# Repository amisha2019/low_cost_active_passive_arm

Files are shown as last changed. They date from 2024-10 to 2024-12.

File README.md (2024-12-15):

# Low-Cost Robot Arm 

This repository contains the files to build and control a low-cost robot arm that costs about $250. You can also build a second robot arm (the leader arm) to control the other arm (the follower arm) that costs about $180, for a total of $430. The design of the leader is inspired by the [GELLO project](https://github.com/wuphilipp/gello_mechanical) but is simpler to build. Such a robot arm is well suited for [robot learning](https://x.com/alexkoch_ai/status/1756500716854841835?s=20). Two of those arms are also capable of [folding clothes](https://x.com/alexkoch_ai/status/1772750496174149708?s=20).

This robot arm uses Dynamixel XL430 and Dynamixel XL330 servo motors. The XL430 motors are almost twice as strong and are used for the first two joints.
The XL330 motors are weaker but weigh only 18g each. This makes the arm very lightweight and fast.
Dynamixel sells the U2D2 adapter to connect the servos to a computer. However, this is very expensive and the latency is very high. This build uses another cheaper adapter board instead.
The robot arm can be controlled with the Dynamixel SDK: ```pip install dynamixel-sdk```

Robot Arm

## Follower Arm

### Required Materials

| Part | Cost | Buying link | Specs |
|---|---|---| --- |
| 2x Dynamixel XL430-W250 | $100 | https://www.robotis.us/dynamixel-xl430-w250-t/ | https://emanual.robotis.com/docs/en/dxl/x/xl430-w250/ |
| 4x Dynamixel XL330-M288 | $96  | https://www.robotis.us/dynamixel-xl330-m288-t/ | https://emanual.robotis.com/docs/en/dxl/x/xl330-m288/|
| XL330 Idler Wheel | $10  | https://www.robotis.us/fpx330-h101-4pcs-set/ | **Note**: pack of four; three needed for  longer version pictured above (with elbow-to-wrist extension), two needed for shorter version|
| XL430 Idler Wheel | $7 | https://www.robotis.us/hn11-i101-set/ | |
| Waveshare Serial Bus Servo Driver Board | $10  | https://a.co/d/7C3RUYU | |
| Voltage Reducer | $10 | https://a.co/d/cy02ADW | **Note**: pack of six, only one needed per follower arm |
| 12V Power Supply | $12  | https://a.co/d/40o8uMN | |
| Table Clamp | $6 | https://a.co/d/4KEiYdV | |
| Wires | $7 | https://a.co/d/hQfk2cb | |
| Total | $258 | | |

There is usually a 10% discount code for the Robotis shop. It might also help to add some grip tape to the gripper (e.g. https://a.co/d/dW7BnEN). A USB-C cable is necessary to connect the servo driver board to a computer.

### Assembly

1. Print all parts with a 3D printer
   1. The STL files are in `hardware/follower/stl`
   2. The parts are designed to be easy to print; only the moving part of the gripper needs supports
2. Scanning motors
   1. Connect the driver board to a computer (should work with Linux and MacOS)
   2. Figure out the device name (e.g. tty.usbmodem57380045631 for MacOS): ```ls /dev/tty.*```
   3. Scan each motor individually with [Dynamixel Wizard](https://emanual.robotis.com/docs/en/software/dynamixel/dynamixel_wizard2/)
      1. Set the baudrate to 1M for all motors
      2. Set the servo IDs to 1 for the shoulder to 5 (6 if using the elbow-to-wrist extension) for the gripper servo
3. Assembly
   1. Assemble the arm without the base
      1. Make sure that the servos are fixed in the same position as in the CAD
      2. The servo horn should be in the default position when screwed in
   2. Solder wires onto voltage reducer; input should be connected to female connectors and the output to male connectors
   3. Screw the voltage reducer and the servo driver board onto the base
   4. Screw the base onto the arm
   5. Connect D, V, and G ports on the driver board to the shoulder rotation servo
   6. Connect the shoulder rotation servo to the shoulder lift servo
   7. Connect the input for the voltage reducer to V and G ports on the driver board
   8. Connect the output of the voltage reducer and the remaining D port of the driver board to the elbow servo
   9. Connect the driver board to the power supply
   10. Connect to an XL330 servo and view the input voltage on Dynamixel Wizard, then adjust the screw on the voltage reducer until the input voltage is 5V

## Leader Arm

### Required Materials

| Part | Cost | Buying link | Specs |
|---|---| --- | --- |
| 6x Dynamixel XL330-M077 | $144 |  https://www.robotis.us/dynamixel-xl330-m077-t/ | https://emanual.robotis.com/docs/en/dxl/x/xl330-m077/|
| XL330 Frame | $7 | https://www.robotis.us/fpx330-s101-4pcs-set/ | |
| XL330 Idler Wheel | $10  | https://www.robotis.us/fpx330-h101-4pcs-set/ | **Note**: pack of four; three needed for longer version (with elbow-to-wrist extension), two needed for shorter version pictured below |
| Waveshare Serial Bus Servo Driver Board | $10  | https://a.co/d/7C3RUYU | |
| 5V Power Supply | $6 | https://a.co/d/5u90NVp | |
| Table Clamp | $6 | https://a.co/d/4KEiYdV | |
| Total | $183 | | |

### Assembly

The assembly of the leader arm is simpler since all motors use 5V. The gripper is replace by a handle and a trigger. During use, a small torque can be applied to the trigger so that it opens by default. The GELLO design uses a spring for this purpose but it is much more difficult to assemble.
The `teleoperation.py` script can be used to test the arms. However, the device names might have to be adjusted.

## Simulation
A basic simulation environment in MuJoCo is available by running `simulation.py`.

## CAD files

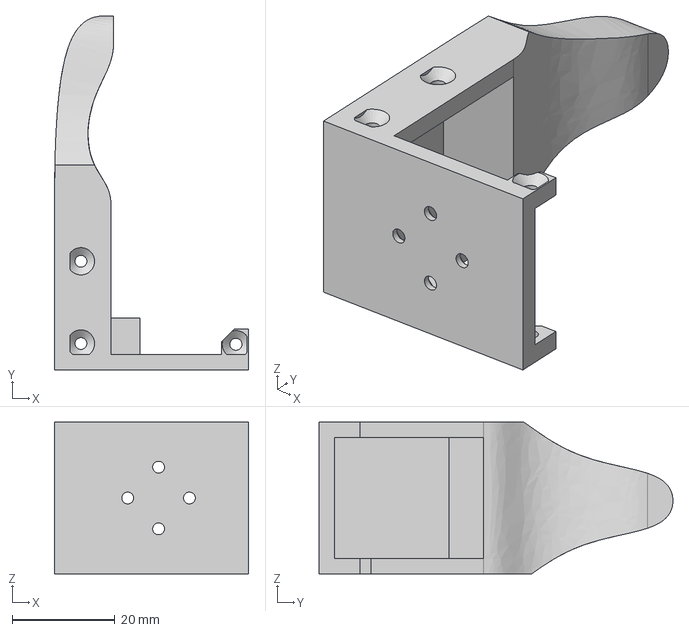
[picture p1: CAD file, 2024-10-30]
hardware/follower/step/gripper_static_part.step
37.7 x 68.9 x 29.5 mm

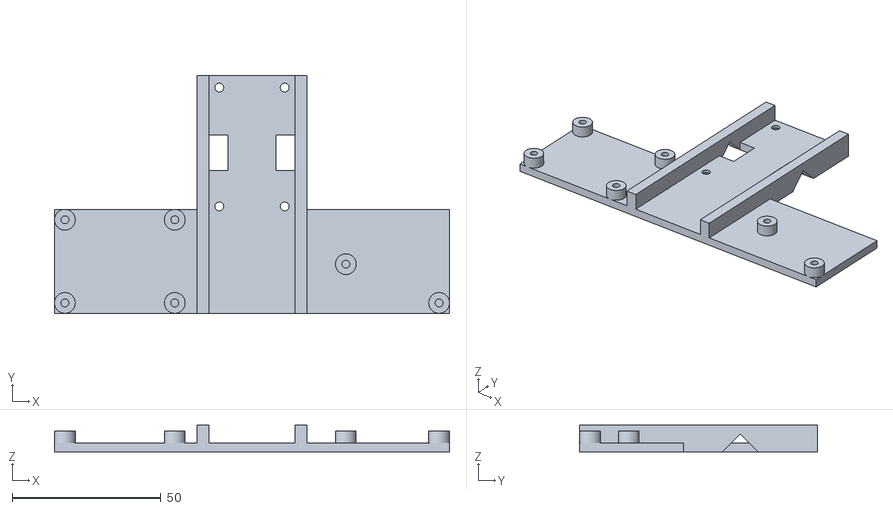
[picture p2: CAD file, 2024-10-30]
hardware/follower/stl/base.stl
133.0 x 80.0 x 9.00

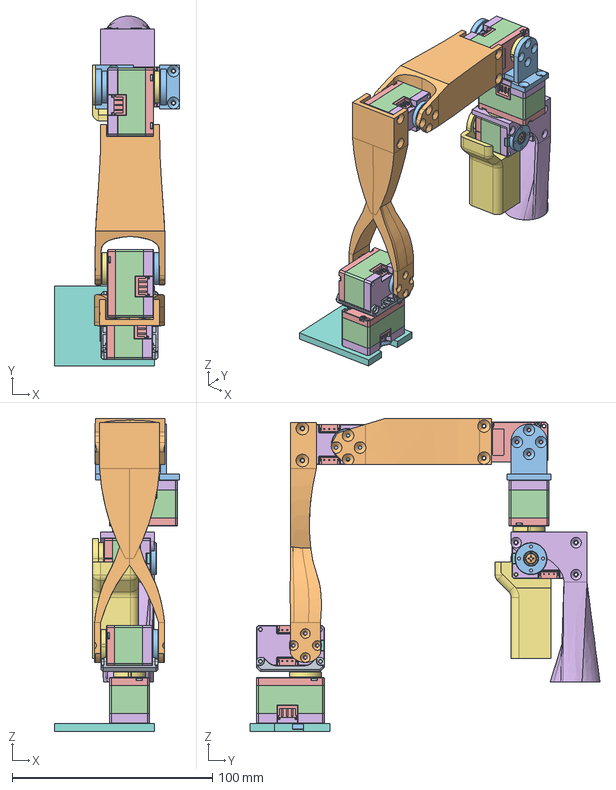
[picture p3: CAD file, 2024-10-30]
hardware/leader/step/leader_arm.step
62.7 x 175.0 x 156.5 mm
Servo Connector redesign
shoulder_rotation
DC15_A01_CASE_M_DUMMY x 6
DC15_A01_CASE_F_DUMMY x 6
DC15_A01_CASE_B_DUMMY x 6
DC15_A01_HORN_DUMMY x 6
DC15_A01_LED_CAP2_DUMMY x 6
PHS_1_7X20_5_DC10 x 24
BTS2_M2_6X8 x 12
DC15_A01_HORN_IDLE2_DUMMY x 6
DC15_A01_IDLE_CAP_DUMMY x 6
B3B-EH x 12
handle
trigger
base
fpx330-s101
connector

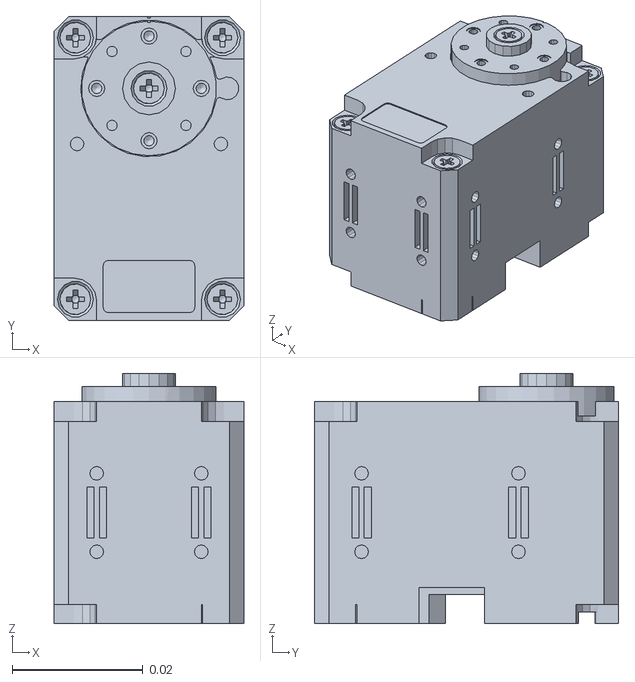
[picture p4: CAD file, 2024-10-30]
simulation/gello_active/assets/gello_active/xl430_2.STL
0.029 x 0.0465 x 0.0383

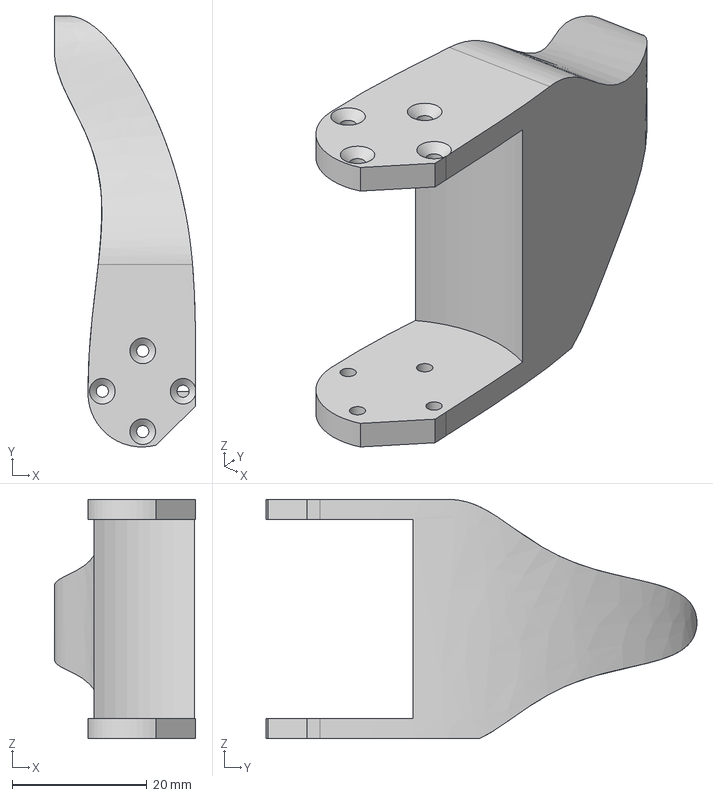
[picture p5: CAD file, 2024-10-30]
hardware/follower/step/gripper_moving_part.step
21.0 x 64.0 x 35.5 mm

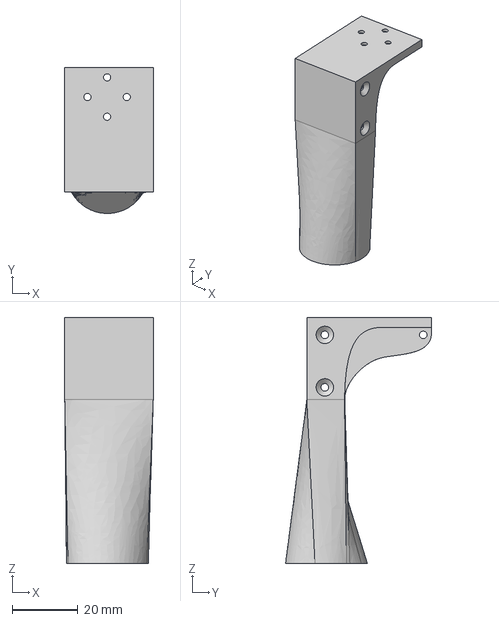
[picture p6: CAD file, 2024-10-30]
hardware/leader/step/gripper_handle.step
27.0 x 44.5 x 75.0 mm

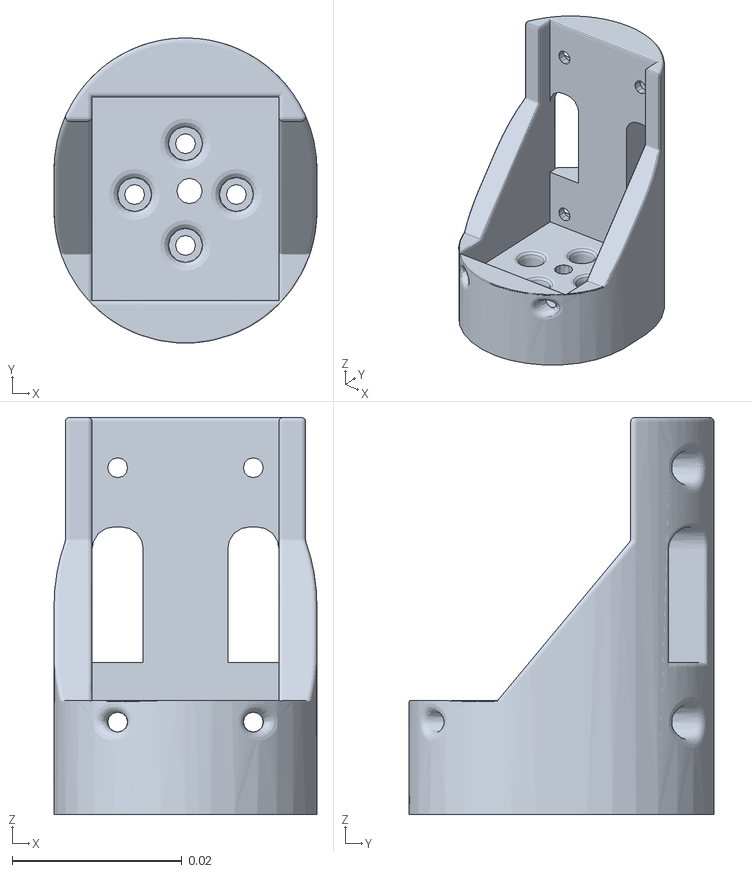
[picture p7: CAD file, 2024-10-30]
simulation/gello_active/assets/gello_active/L4.STL
0.031 x 0.036 x 0.0468

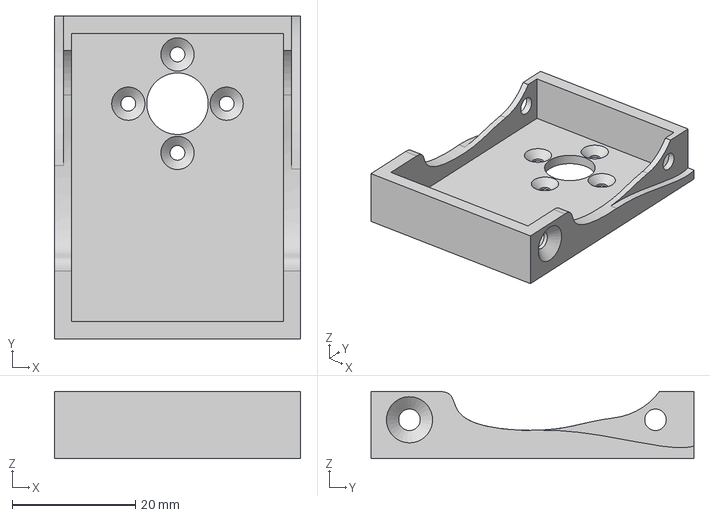
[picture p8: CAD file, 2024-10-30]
hardware/follower/step/shoulder_rotation.step
40.0 x 52.5 x 10.9 mm

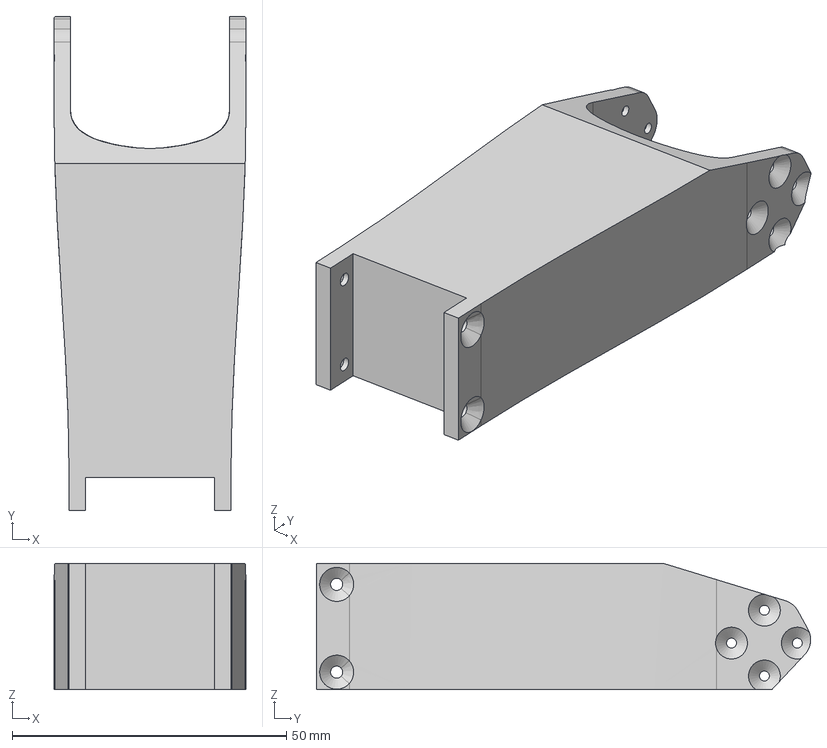
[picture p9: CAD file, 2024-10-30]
hardware/leader/step/elbow_to_wrist_extension.step
35.0 x 90.1 x 23.0 mm

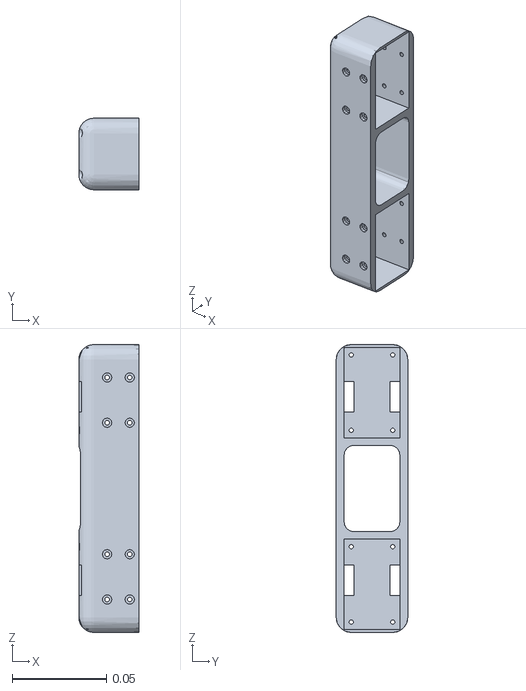
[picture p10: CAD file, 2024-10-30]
simulation/gello_active/assets/gello_active/L2.STL
0.032 x 0.038 x 0.153

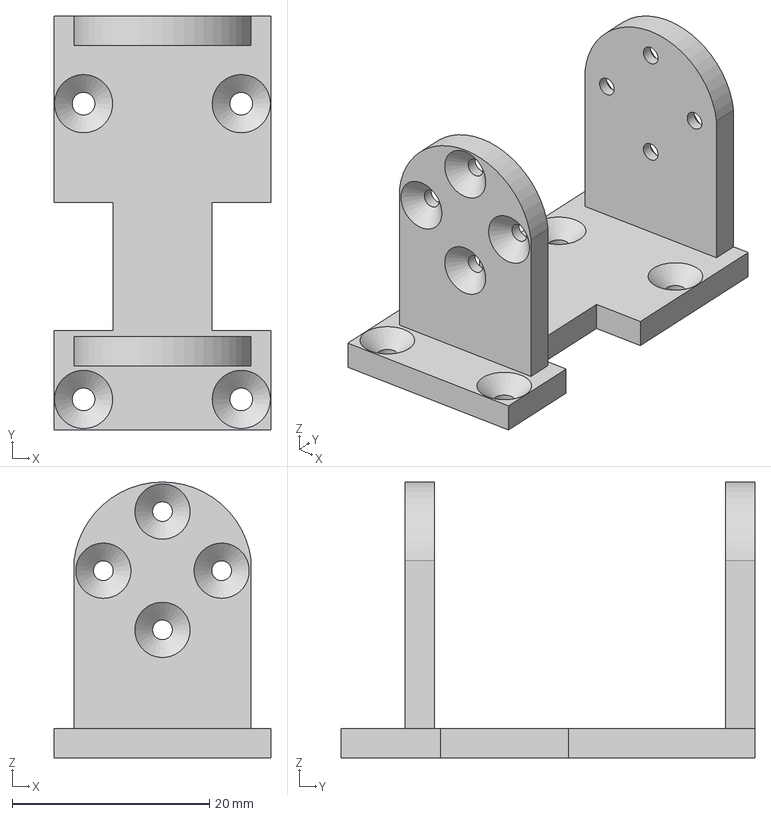
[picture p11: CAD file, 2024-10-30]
hardware/follower/step/elbow_to_wrist.step
22.0 x 42.0 x 28.0 mm

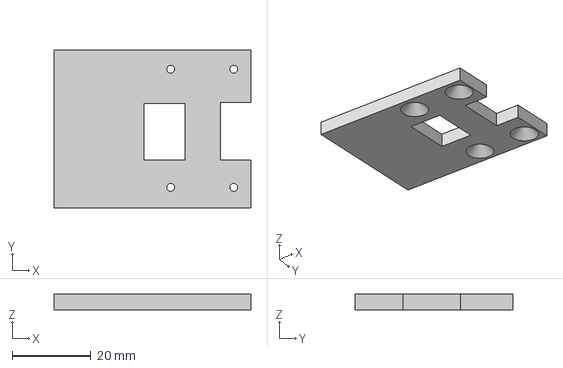
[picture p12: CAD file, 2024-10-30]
hardware/leader/step/base.step
50.0 x 40.0 x 4.00 mm

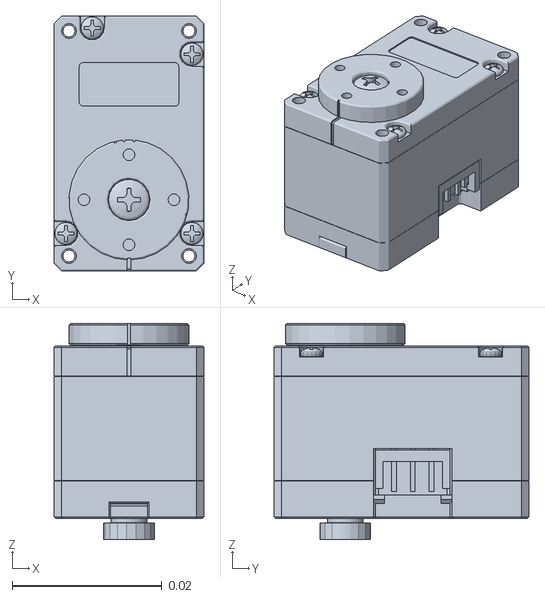
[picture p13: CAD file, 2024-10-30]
simulation/gello_active/assets/gello_active/xl330_3.STL
0.02 x 0.034 x 0.0288

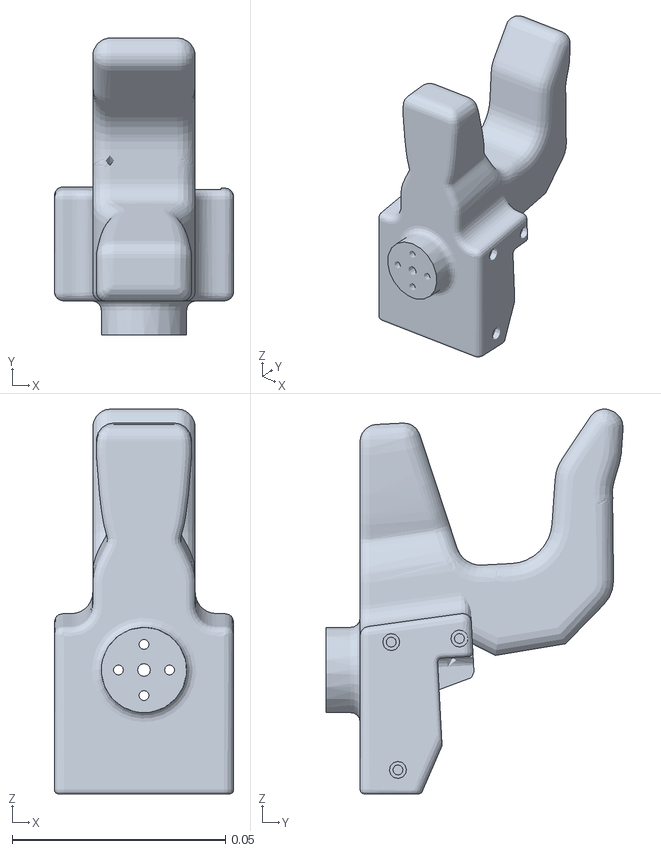
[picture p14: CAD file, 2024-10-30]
simulation/gello_active/assets/gello_active/end_effector.STL
0.042 x 0.0696 x 0.0902

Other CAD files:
hardware/leader/step/elbow_to_wrist.step
hardware/follower/step/arm.step
hardware/leader/step/shoulder_to_elbow.step
hardware/follower/follower_arm.f3z
hardware/follower/step/shoulder_to_elbow.step
hardware/follower/stl/elbow_to_wrist.stl
hardware/follower/stl/elbow_to_wrist_extension.stl
hardware/follower/stl/gripper_moving_part.stl
hardware/follower/stl/gripper_static_part.stl
hardware/follower/stl/shoulder_rotation.stl
hardware/follower/stl/shoulder_to_elbow.stl
hardware/leader/leader_arm.f3z
hardware/leader/step/gripper_trigger.step
hardware/leader/stl/base.stl
hardware/leader/stl/elbow_to_wrist.stl
hardware/leader/stl/elbow_to_wrist_extension.stl
hardware/leader/stl/gripper_handle.stl
hardware/leader/stl/gripper_trigger.stl
hardware/leader/stl/shoulder_to_elbow.stl
simulation/gello_active/assets/gello_active/L1.STL
simulation/gello_active/assets/gello_active/L3.STL
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

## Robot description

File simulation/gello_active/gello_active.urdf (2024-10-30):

<?xml version="1.0" encoding="utf-8"?>
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
<robot name="gello_active">
  <link name="base_link">
    <inertial>
      <origin xyz="0.00607992357022163 0.00301681012562898 -0.0120084237052049" rpy="0 0 0" />
      <mass value="0.141701823329413" />
      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
    </inertial>
    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
  </link>
  <link name="xl430_1">
    <inertial>
      <origin xyz="1.5967816055059E-05 -0.0231678735095451 0.189804632480122" rpy="0 0 0" />
      <mass value="0.0422899908141637" />
      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
    </inertial>
    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
  </link>
  <joint name="base_fix_joint" type="fixed">
    <origin xyz="0.031148 0.02289 -0.18013" rpy="0 0 0" />
    <parent link="base_link" />
    <child link="xl430_1" />
    <axis xyz="0 0 0" />
  </joint>
  <link name="L1">
    <inertial>
      <origin xyz="0.0131095359774512 0.0200185962795386 3.85052656877438E-08" rpy="0 0 0" />
      <mass value="0.0422302330046642" />
      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
    </inertial>
    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
  </link>
  <joint name="shoulder_pan_joint" type="continuous">
    <origin xyz="0 -0.011 0.20764" rpy="1.5708 0 1.5588" />
    <parent link="xl430_1" />
    <child link="L1" />
    <axis xyz="0 1 0" />
  </joint>
  <link name="xl430_2">
    <inertial>
      <origin xyz="1.59678160428812E-05 -0.0121678735095403 -0.0205450583333916" rpy="0 0 0" />
      <mass value="0.0422899908141372" />
      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
    </inertial>
    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
  </link>
  <joint name="shoulder_lift_joint" type="continuous">
    <origin xyz="0.03915 0.021935 0" rpy="1.5708 1.5675 -1.5708" />
    <parent link="L1" />
    <child link="xl430_2" />
    <axis xyz="0 0 1" />
  </joint>
  <link name="L2">
    <inertial>
      <origin xyz="0.0177542994227649 2.65439271743273E-08 -0.0453750285135328" rpy="0 0 0" />
      <mass value="0.0546858829355452" />
      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
    </inertial>
    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
  </link>
  <joint name="L2_fix_joint_1" type="fixed">
    <origin xyz="0 -0.0178 -0.04565" rpy="1.5708 -1.5708 3.14" />
    <parent link="xl430_2" />
    <child link="L2" />
    <axis xyz="0 0 0" />
  </joint>
  <link name="xl430_3">
    <inertial>
      <origin xyz="1.59678160644369E-05 -0.0231678735095394 0.189804632480152" rpy="0 0 0" />
      <mass value="0.0422899908141366" />
      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
    </inertial>
    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
  </link>
  <joint name="L2_fix_joint_2" type="fixed">
    <origin xyz="-0.1647 0 -0.11955" rpy="-1.5708 0 -1.5708" />
    <parent link="L2" />
    <child link="xl430_3" />
    <axis xyz="0 0 0" />
  </joint>
  <link name="L3">
    <inertial>
      <origin xyz="-0.0301727625382926 7.29364901808083E-09 0.0367965289329686" rpy="0 0 0" />
      <mass value="0.0492342604004969" />
      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
    </inertial>
    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
  </link>
  <joint name="elbow_joint" type="continuous">
    <origin xyz="0 -0.011 0.20635" rpy="3.1391 1.5708 0" />
    <parent link="xl430_3" />
    <child link="L3" />
    <axis xyz="1 0 0" />
  </joint>
  <link name="xl330_1">
    <inertial>
      <origin xyz="0.075420933410812 0.0347673256207063 0.382628050770604" rpy="0 0 0" />
      <mass value="0.0152279846230564" />
      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
    </inertial>
    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
  </link>
  <joint name="L3_fix_joint" type="fixed">
    <origin xyz="-0.4171 0.075425 0.13419" rpy="-1.5708 0 -1.5708" />
    <parent link="L3" />
    <child link="xl330_1" />
    <axis xyz="0 0 0" />
  </joint>
  <link name="L4">
    <inertial>
      <origin xyz="-0.000477072229915942 0.00401650330059737 0.0139990913771146" rpy="0 0 0" />
      <mass value="0.0140660643273876" />
      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
    </inertial>
    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
  </link>
  <joint name="wrist1_joint" type="continuous">
    <origin xyz="0.075425 0.027592 0.39603" rpy="0 0 -0.0253" />
    <parent link="xl330_1" />
    <child link="L4" />
    <axis xyz="0 0 1" />
  </joint>
  <link name="xl330_2">
    <inertial>
      <origin xyz="0.0754209334106387 0.0347673256204681 0.38262805076857" rpy="0 0 0" />
      <mass value="0.0152279846189667" />
      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
    </inertial>
    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
  </link>
  <joint name="L4_fix_joint" type="fixed">
    <origin xyz="0.07495 0.38155 0.061433" rpy="-1.5708 0 -3.1416" />
    <parent link="L4" />
    <child link="xl330_2" />
    <axis xyz="0 0 0" />
  </joint>
  <link name="L5">
    <inertial>
      <origin xyz="-0.00366525305716781 -0.0146866156468189 -5.58749708168271E-08" rpy="0 0 0" />
      <mass value="0.0143126365472127" />
      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
    </inertial>
    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
  </link>
  <joint name="wrist2_joint" type="continuous">
    <origin xyz="0.075425 0.027592 0.39554" rpy="-1.5708 0 0.0015559" />
    <parent link="xl330_2" />
    <child link="L5" />
    <axis xyz="0 1 0" />
  </joint>
  <link name="xl330_3">
    <inertial>
      <origin xyz="0.0754209334109733 0.034767325620958 0.382628050772475" rpy="0 0 0" />
      <mass value="0.0152279846267835" />
      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
    </inertial>
    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
  </link>
  <joint name="L5_fix_joint" type="fixed">
    <origin xyz="-0.38197 -0.06135 0.075425" rpy="0 1.5708 0" />
    <parent link="L5" />
    <child link="xl330_3" />
    <axis xyz="0 0 0" />
  </joint>
  <link name="end_effector">
    <inertial>
      <origin xyz="-0.000754673739559147 0.0314156499838131 0.019054370079741" rpy="0 0 0" />
      <mass value="0.0630826138989227" />
      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
    </inertial>
    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
  </link>
  <joint name="end_effector_joint" type="continuous">
    <origin xyz="0.075425 0.027592 0.39645" rpy="1.5708 0 -0.0035937" />
    <parent link="xl330_3" />
    <child link="end_effector" />
    <axis xyz="0 1 0" />
  </joint>
</robot>

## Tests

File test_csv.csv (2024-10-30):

shoulder_pan_angle | shoulder_lift_angle | elbow_angle | wrist1_angle | wrist2_angle | wrist3_angle | end_eff_x | end_eff_y | end_eff_z | end_eff_roll | end_eff_pitch | end_eff_yaw | end_eff_w | end_eff_xq | end_eff_yq | end_eff_zq | gripper_pos
-1.595508877431051 | -1.5983616314330042 | -1.596028447151184 | -1.5511920370957633 | 1.5769364833831787 | 1.5969127416610718 | 0.023529411764705882 | -0.13866740569922242 | -0.2984518748763483 | 0.28981716946903796 | -2.2654083880941385 | -2.149327141193777 | -0.04694173033470125 | 0.023529411764705882 | 0.023529411764705882
-1.5942290464984339 | -1.5983792744078578 | -1.59576416015625 | -1.5510205545327445 | 1.5769202709197998 | 1.596408486366272 | 0.023529411764705882 | -0.1381336836522397 | -0.2987266204661276 | 0.28984151784709505 | -2.2629313974454437 | -2.1521077248571445 | -0.04675525879796806 | 0.023529411764705882 | 0.023529411764705882
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

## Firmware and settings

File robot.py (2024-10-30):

#!/usr/bin/env python3
import numpy as np
from dynamixel import Dynamixel, OperatingMode, ReadAttribute
import time
from dynamixel_sdk import GroupSyncRead, GroupSyncWrite, DXL_LOBYTE, DXL_HIBYTE, DXL_LOWORD, DXL_HIWORD
from enum import Enum, auto
from typing import Union

class MotorControlType(Enum):
    PWM = auto()
    POSITION_CONTROL = auto()
    DISABLED = auto()
    UNKNOWN = auto()

class Robot:
    def __init__(self, dynamixel, baudrate=1000000, servo_ids=[1, 2, 3, 4, 5]):
        self.servo_ids = servo_ids
        self.dynamixel = dynamixel
        
        self.position_reader = GroupSyncRead(
            self.dynamixel.portHandler,
            self.dynamixel.packetHandler,
            ReadAttribute.POSITION.value,
            4
        )
        for id in self.servo_ids:
            self.position_reader.addParam(id)

        self.velocity_reader = GroupSyncRead(
            self.dynamixel.portHandler,
            self.dynamixel.packetHandler,
            ReadAttribute.VELOCITY.value,
            4
        )
        for id in self.servo_ids:
            self.velocity_reader.addParam(id)

        self.pos_writer = GroupSyncWrite(
            self.dynamixel.portHandler,
            self.dynamixel.packetHandler,
            self.dynamixel.ADDR_GOAL_POSITION,
            4
        )
        for id in self.servo_ids:
            self.pos_writer.addParam(id, [2048])

        self.pwm_writer = GroupSyncWrite(
            self.dynamixel.portHandler,
            self.dynamixel.packetHandler,
            self.dynamixel.ADDR_GOAL_PWM,
            2
        )
        for id in self.servo_ids:
            self.pwm_writer.addParam(id, [2048])

        self._disable_torque()
        self.motor_control_state = MotorControlType.DISABLED

    def read_position(self, tries=2):
        result = self.position_reader.txRxPacket()
        if result != 0:
            if tries > 0:
                return self.read_position(tries=tries - 1)
            else:
                print("failed to read position!!!!!!!!!!!!!!!!!!!!!!!!!!!!!")
        positions = []
        for id in self.servo_ids:
            position = self.position_reader.getData(id, ReadAttribute.POSITION.value, 4)
            if position > 2 ** 31:
                position -= 2 ** 32
            positions.append(position)
        return positions

    def read_velocity(self):
        self.velocity_reader.txRxPacket()
        velocities = []
        for id in self.servo_ids:
            velocity = self.velocity_reader.getData(id, ReadAttribute.VELOCITY.value, 4)
            if velocity > 2 ** 31:
                velocity -= 2 ** 32
            velocities.append(velocity)
        return velocities

    def set_goal_pos(self, action):
        if self.motor_control_state is not MotorControlType.POSITION_CONTROL:
            self._set_position_control()
        for i, motor_id in enumerate(self.servo_ids):
            data_write = [DXL_LOBYTE(DXL_LOWORD(action[i])),
                          DXL_HIBYTE(DXL_LOWORD(action[i])),
                          DXL_LOBYTE(DXL_HIWORD(action[i])),
                          DXL_HIBYTE(DXL_HIWORD(action[i]))]
            self.pos_writer.changeParam(motor_id, data_write)
        self.pos_writer.txPacket()

    def set_pwm(self, action):
        if self.motor_control_state is not MotorControlType.PWM:
            self._set_pwm_control()
        for i, motor_id in enumerate(self.servo_ids):
            data_write = [DXL_LOBYTE(DXL_LOWORD(action[i])),
                          DXL_HIBYTE(DXL_LOWORD(action[i]))]
            self.pwm_writer.changeParam(motor_id, data_write)
        self.pwm_writer.txPacket()

    def set_trigger_torque(self):
        self.dynamixel._enable_torque(self.servo_ids[-1])
        self.dynamixel.set_pwm_value(self.servo_ids[-1], 200)

    def limit_pwm(self, limit: Union[int, list, np.ndarray]):
        if isinstance(limit, int):
            limits = [limit] * 5
        else:
            limits = limit
        self._disable_torque()
        for motor_id, limit in zip(self.servo_ids, limits):
            self.dynamixel.set_pwm_limit(motor_id, limit)
        self._enable_torque()

    def _disable_torque(self):
        print(f'disabling torque for servos {self.servo_ids}')
        for motor_id in self.servo_ids:
            self.dynamixel._disable_torque(motor_id)

    def _enable_torque(self):
        print(f'enabling torque for servos {self.servo_ids}')
        for motor_id in self.servo_ids:
            self.dynamixel._enable_torque(motor_id)

    def _set_pwm_control(self):
        self._disable_torque()
        for motor_id in self.servo_ids:
            self.dynamixel.set_operating_mode(motor_id, OperatingMode.PWM)
        self._enable_torque()
        self.motor_control_state = MotorControlType.PWM

    def _set_position_control(self):
        self._disable_torque()
        for motor_id in self.servo_ids:
            self.dynamixel.set_operating_mode(motor_id, OperatingMode.POSITION)
        self._enable_torque()
        self.motor_control_state = MotorControlType.POSITION_CONTROL

if __name__ == "__main__":
    robot = Robot(dynamixel=Dynamixel(device_name='/dev/tty.usbmodem57380045631'))
    robot._disable_torque()
    for _ in range(10000):
        s = time.time()
        pos = robot.read_position()
        elapsed = time.time() - s
        print(f'read took {elapsed} pos {pos}')

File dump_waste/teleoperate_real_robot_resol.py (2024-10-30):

from robot import Robot
from dynamixel import Dynamixel
from get_hardware_offset import ArmOffset
import numpy as np
import time

leader_device= "/dev/serial/by-id/usb-FTDI_USB__-__Serial_Converter_FT8ISI2Y-if00-port0"
follower_device = "/dev/serial/by-id/usb-FTDI_USB__-__Serial_Converter_FT8J0W3F-if00-port0"

## Follower Arm Start pos correction
home_pos_correction = np.array([-1.57, 1.57,  3.14, -1.57, -3.14,  0])

## ----- Activate Leader Arm ---------
# leader_armoffset = ArmOffset(device_name=leader_device, baudrate=57600)
# leader_correction_joints = leader_armoffset.correction_joints
# leader_dynamixel = Dynamixel.Config(baudrate=57600, device_name=leader_device).instantiate()
# for i in range(1, 7):
#     leader_dynamixel.set_velocity_limit(i, 10)

## ----- Activate Follower Arm ---------
# follower_armoffset = ArmOffset(device_name=follower_device, baudrate=57600)
# follower_correction_joints = follower_armoffset.correction_joints
follower_dynamixel = Dynamixel.Config(baudrate=57600, device_name=follower_device).instantiate()

# leader = Robot(leader_dynamixel, servo_ids=[1, 2, 3, 4, 5, 6])
for i in range(1, 7):
    follower_dynamixel.set_velocity_limit(i, 10)
follower = Robot(follower_dynamixel, servo_ids=[1, 2, 3, 4, 5, 6])


def resol_2_rad(angles_resol):
    angles_rad = (angles_resol / 2048 - 1) * 3.14
    angles_rad[1] = -angles_rad[1]
    angles_rad[3] = -angles_rad[3]
    angles_rad[4] = -angles_rad[4]
    return angles_rad

def rad_2_resol(angles_rad):
    angles_rad[1] = -angles_rad[1]
    angles_rad[3] = -angles_rad[3]
    angles_rad[4] = -angles_rad[4]
    angles_resol = (angles_rad / 3.14 + 1) * 2048
    return angles_resol

def get_angles_to_publish_rad(angles_rad):
    corrected_joint_rad = angles_rad + home_pos_correction
    corrected_joint_rad[1] = -corrected_joint_rad[1]
    corrected_joint_rad[3] = -corrected_joint_rad[3]
    corrected_joint_rad[4] = -corrected_joint_rad[4]
    return corrected_joint_rad

# def read_leader_position():
#     global leader_joints
#     leader_joints = leader.read_position()
#     leader_joints = np.array(leader_joints)        
#     leader_joints_rad = resol_2_rad(leader_joints)
#     print("Actual resol: ", leader_joints)
#     print("Actual angle: ", leader_joints_rad)
#     leader_joints_rad = (leader_joints_rad - leader_correction_joints)
#     # leader_joints_rad_ = [math.fmod(x, 3.14) for x in leader_joints_rad]
#     print("Actual corrected angle: ", leader_joints_rad)

#     return leader_joints_rad

def set_follower_position(joints_rad):
    # Correct the radians of the follower
    pass

def go_to_start_position():
    start_pos = np.array([-1.57, -1.57, -2, -1.57, 1.57, 1.57])

    # Correct the radians of the leader
    corrected_joint_rad = get_angles_to_publish_rad(start_pos)
    follower_joints_resol = np.array(rad_2_resol(corrected_joint_rad), dtype=int)
    
    print("reading: ", follower.read_position())
    # leader_joints_rad = resol_2_rad(np.array(follower.read_position()))
    # print("Reding rad: ", leader_joints_rad)

    print("Joints to publish rad: ", corrected_joint_rad)
    print("Joints to publish: ", (follower_joints_resol))
    
    #### ____DANGER ZONE____ ####
    ## Read Current Position - Follower - [set Home position]
    # curr_pos = follower.read_position()
    # print("Current Pos: ", curr_pos)
    # print("Going to Home Pose: ")    
    # for i in range(0, len(curr_pos)):
    #     print(f"Curr_Pose_joint{i+1}: {curr_pos[i]}")
    #     curr_pos[i] = follower_joints_resol[i]  
    #     print(f"Set_Pose_joint{i+1}: {curr_pos[i]}")
    #     follower.set_goal_pos(curr_pos)
    #     print(f"{i+1}: done")
    #     time.sleep(2)        
    # print("final Pose")
    # print(resol_2_rad(np.array(follower.read_position())))
    # follower._disable_torque()


while True:
    # follower.set_goal_pos(leader.read_position())
    # Get Leader Arm pos in radians
    # joints_rad = read_leader_position()
    # print("Passive Arm: ", joints_rad)

    # Set Follower Arm pos in radians
    go_to_start_position()
    break
    # read_leader_position()
    # read_leader_position()
    # print(leader.read_position())

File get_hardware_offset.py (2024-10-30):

from robot import Robot
from dynamixel import Dynamixel
import numpy as np
import time
import mujoco.viewer
from simulation.interface import SimulatedRobot
import threading

class ArmOffset:
    def __init__(self, device_name, baudrate):
        self.device_name  = device_name
        self.baudrate = baudrate

        leader_dynamixel = Dynamixel.Config(baudrate=baudrate, device_name= device_name).instantiate()
        self.leader = Robot(leader_dynamixel, servo_ids=[1, 2, 3, 4, 5, 6])

        current_pos =  self.read_position()
        
        print("Current Position: ", current_pos)

        # Round to the nearest multiple of pi/2
        rounded_values = np.round(current_pos / (np.pi / 2)) * (np.pi / 2)

        # Current joints in the specific configuration
        rounded_curr_pos = np.round(rounded_values, 2)

        # Joints in a specific configurations
        self.reset_joints = np.array([-1.57, -1.57, -1.57, -1.57, 1.57, 1.57])

        # Correction required
        self.correction_joints = rounded_curr_pos - self.reset_joints

    def read_position(self):
        global target_pos

        target_pos = np.array(self.leader.read_position())
        target_pos = (target_pos / 2048 - 1) * 3.14
        target_pos[1] = -target_pos[1]
        target_pos[3] = -target_pos[3]
        target_pos[4] = -target_pos[4]
        return target_pos





    # Always subtract the correction joints from the current joints
    # print("Offset: ", rounded_curr_pos)
    # print("Corrections: ", correction_joints)  
    # print("After Correction: ", rounded_curr_pos - correction_joints)
